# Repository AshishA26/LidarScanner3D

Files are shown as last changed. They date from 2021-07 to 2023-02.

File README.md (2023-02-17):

# LidarScanner3D

I designed and implemented a system from scratch which allows you to map a point cloud of your environment and nearby objects using LIDAR, Arduino, and Unreal Engine 4. 

I made the real time visualization tool using Unreal Engine and interfaced the LIDAR with an Arduino Mega using UART and I2C communication protocols.

In order for the Arduino to communicate with Unreal Engine 4, I used the "UE4Duino" plugin created by [RVillani](https://github.com/RVillani/UE4Duino).

Example scan of a sofa using a Lidar Lite-V3 (the white color in the middle is the location of the scanning system):
LiteV3LoadGif

Demonstration of the Lidar rotation with real-time mapping display:
ScanningGif

## Instructions to Run
- Hook everything up to the Arduino according to the [circuit  diagrams below](#circuit-diagrams)
- Upload the appropriate Arduino code, depending on which LIDAR you are using
- Run the `LidarScanner.exe` application, specify `Com Port`, `baud rate`, `scan type` and go from there

*Note: The `exe` is available in the releases of this repository.*

## Help/Tips
When trying to load a previously saved scan into Unreal Engine 4 project:
- Remember to rename the `.sav` file to `ScanDataSave.sav`
- The file goes in `.\LidarScanner3D\LidarScannerUE4\Saved\SaveGames`

When trying to load a previously saved scan into the compiled `LidarScanner.exe`:
- Go to `.\LidarScannerUE4Compiled\LidarScanner\Saved\SaveGames` and find `ScanDataSave.sav`
    - Note: This file has the point cloud data
- If wanted, copy or move it out into a different folder to keep for later and can rename it to something like `room.sav`
- To load back in, name the file as `ScanDataSave.sav` and move it to the `SaveGames` folder

## Mechanical Design 
Although I made the [first prototype out of wood](./Pics/LidarScannerPic5.jpg), the final design for the Lidar pan-and-tilt was hand built from Aluminum plates. It allows for easy portability, rotation, and great stability.

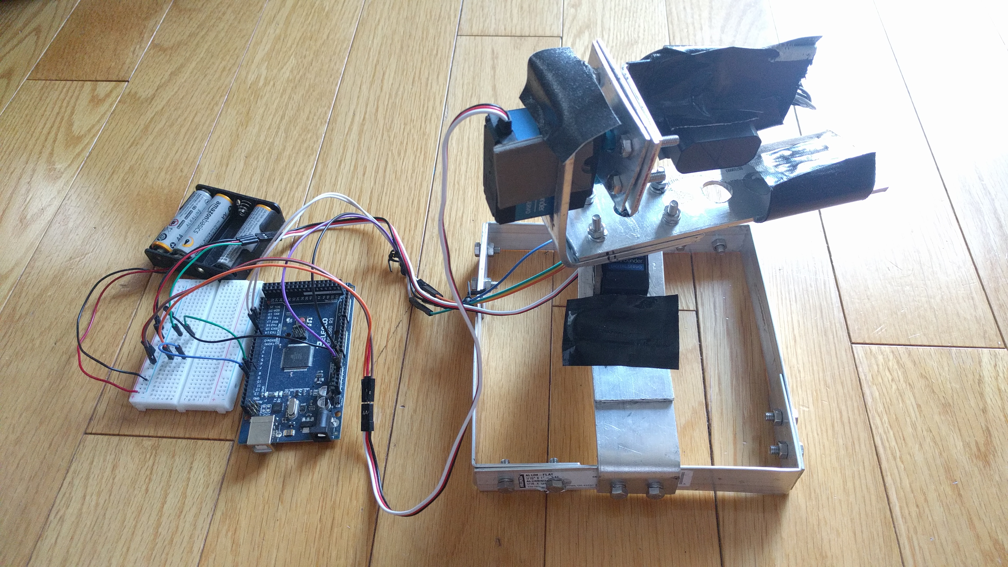
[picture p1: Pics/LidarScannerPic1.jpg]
LidarScannerPic1


There are 2 servos needed in order to achieve the scan. Servo 1 is placed right side up allowing the Lidar to rotate horizontally from side to side, and Servo 2 is placed sideways on Servo 1 allowing the Lidar to tilt vertically. To achieve a scan that fixes the tilt in the placement data, calculations have been done as shown [below](#point-calculations).

## Circuit Diagrams

I have interfaced the Lidar Lite V3 and TFMini Plus Lidar range finders with an Arduino Mega. I chose to do this using a perfboard for easy development and modularity. Some circuit schematics I made in Fritzing are shown below:

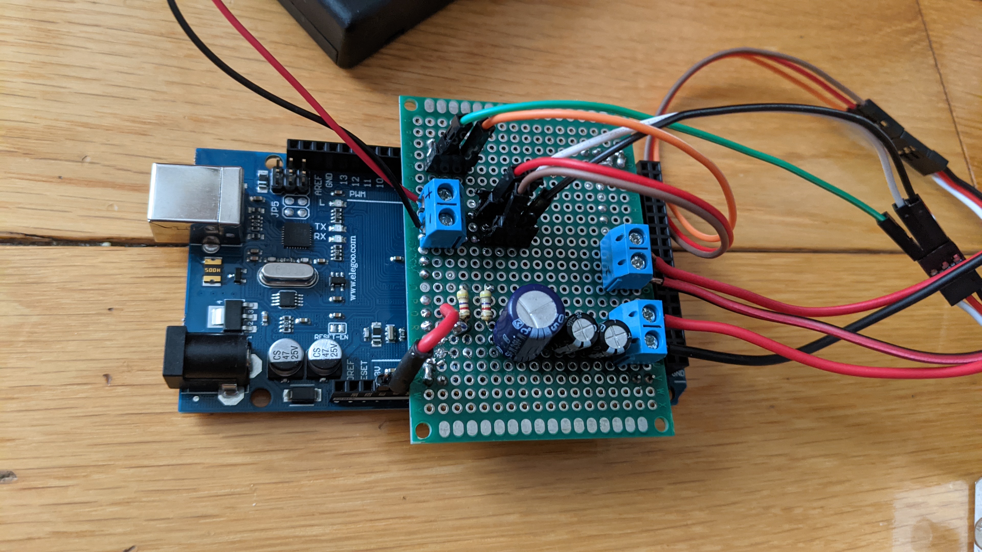
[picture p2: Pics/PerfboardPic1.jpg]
CircuitPicture


For Lidar Lite V3 using perfboard:
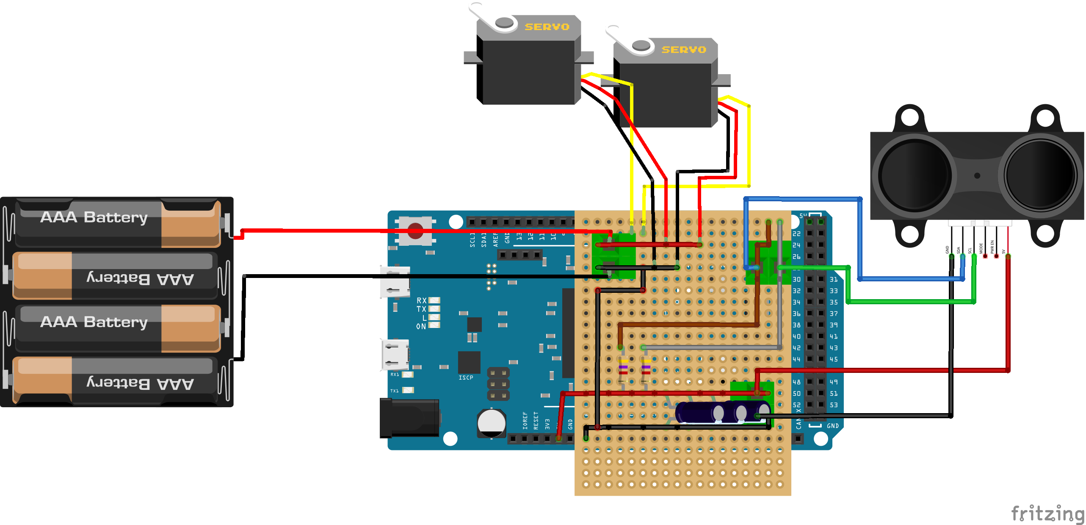
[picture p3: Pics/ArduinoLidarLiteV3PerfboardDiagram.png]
ArduinoLidarLiteV3PerfboardDiagram


For Lidar Lite V3 using breadboard:
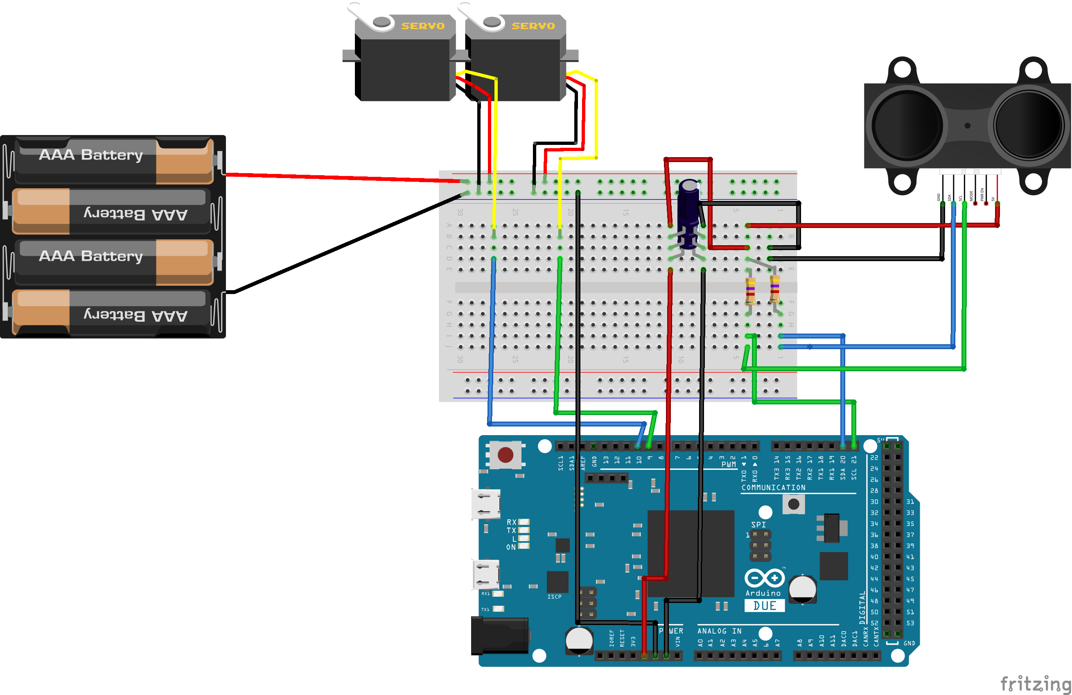
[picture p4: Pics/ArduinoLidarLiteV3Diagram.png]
ArduinoLidarLiteV3Diagram


For TFMini Plus:
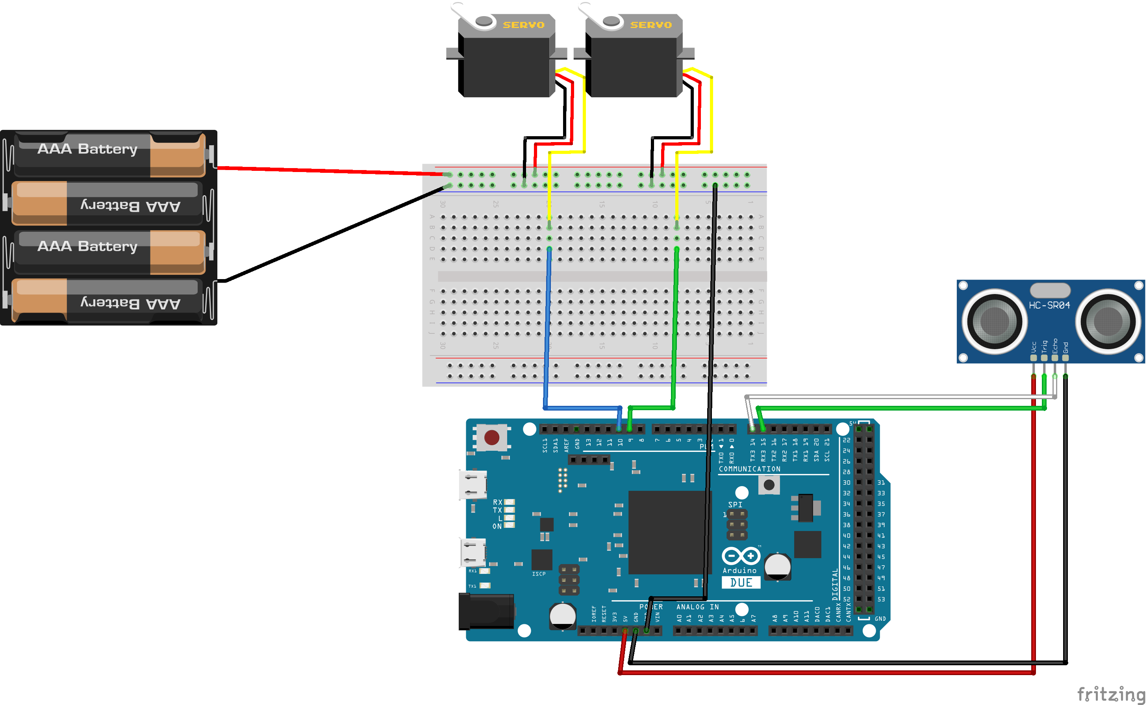
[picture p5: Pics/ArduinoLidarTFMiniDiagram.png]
ArduinoLidarTFMiniDiagram

 (Note: Replace the Sonar in the diagram with a TFMini Plus. The wiring from the TFMini Plus is based on the colors in the diagram).

For more pictures and diagrams, see the [Pics folder](https://github.com/AshishA26/LidarScanner3D/tree/main/Pics) of this repo.

## Point calculations
The LIDAR sensor measures a distance to the object, and the current orientation of this sensor is given by the servo positions. The angle calculations I did for finding the exact location of the point relative to the LIDAR in 3D Space using vector geometry are shown below:
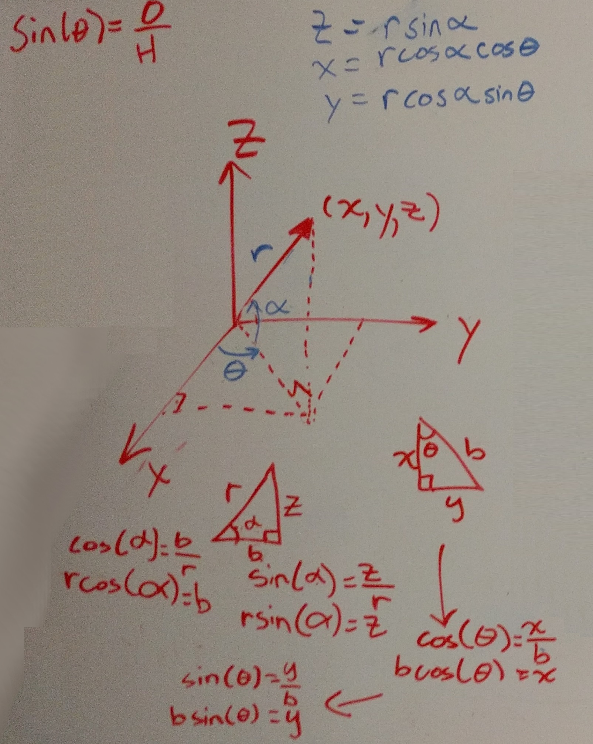
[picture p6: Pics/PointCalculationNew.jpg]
PointCalculation


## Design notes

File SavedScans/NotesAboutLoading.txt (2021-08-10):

When trying to load:
- Remember to rename the .sav file to ScanDataSave.sav
- It goes in \LidarScanner3D\LidarScannerUE4\Saved\SaveGames

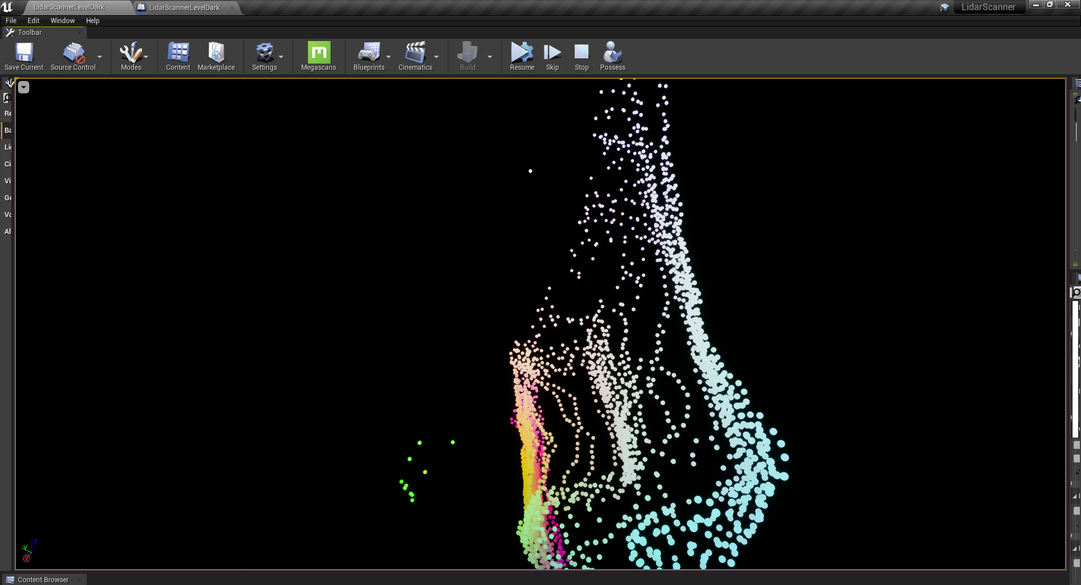
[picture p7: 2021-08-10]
Pics/Scans/sofa5b.png

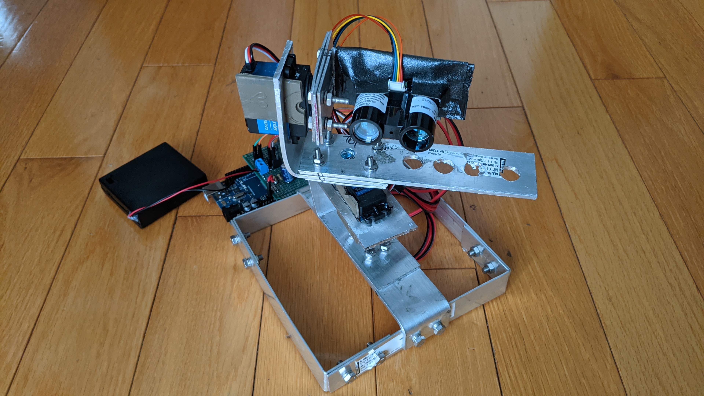
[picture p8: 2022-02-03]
Pics/LidarScannerPic2.jpg

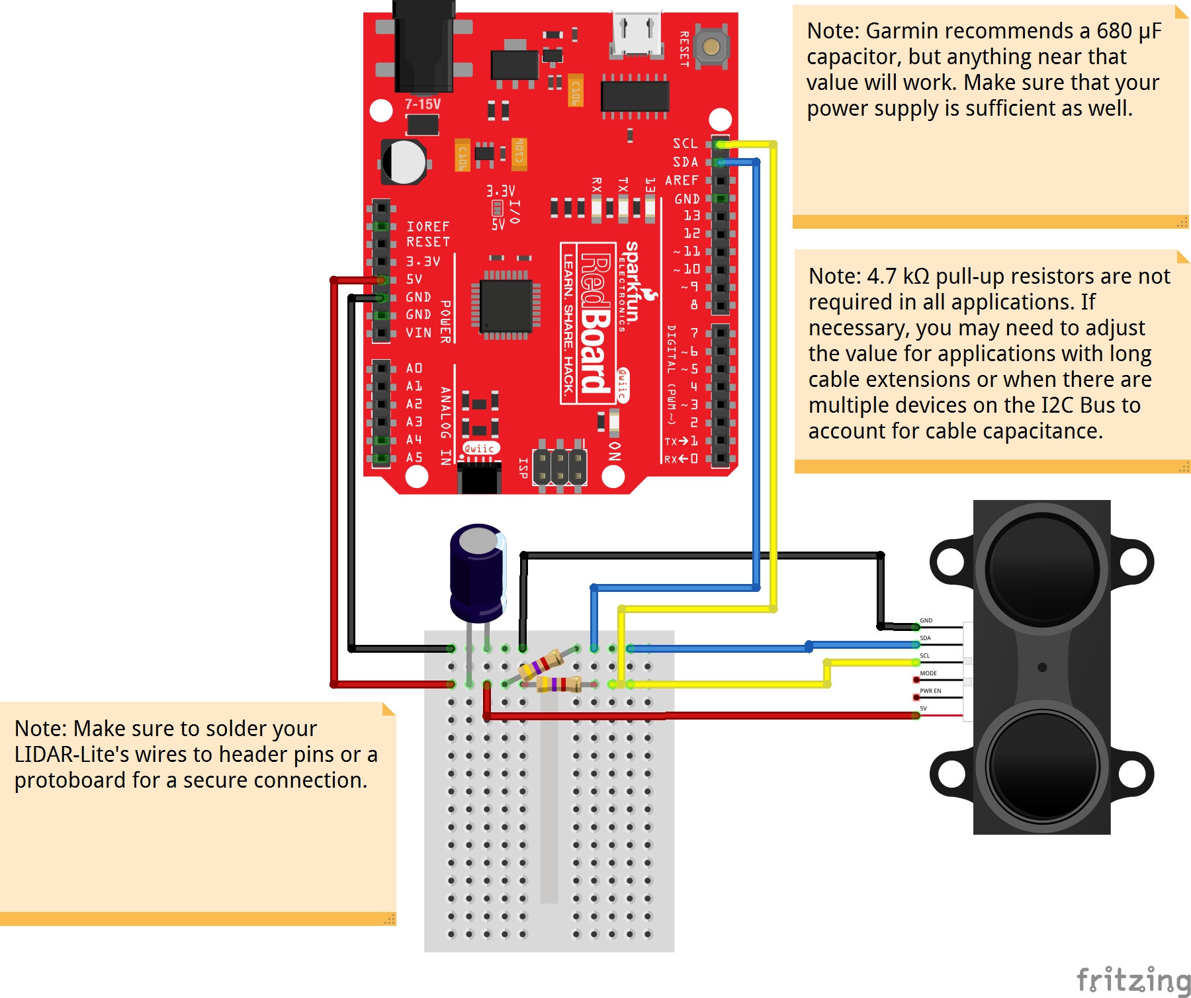
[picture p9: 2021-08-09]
Pics/SparkfunLidarV3Diagram.jpg

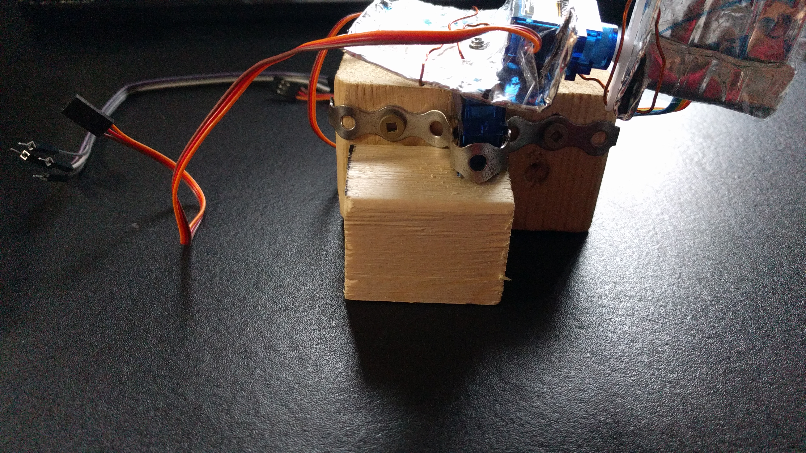
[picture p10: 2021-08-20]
Pics/LidarScannerPic3.jpg

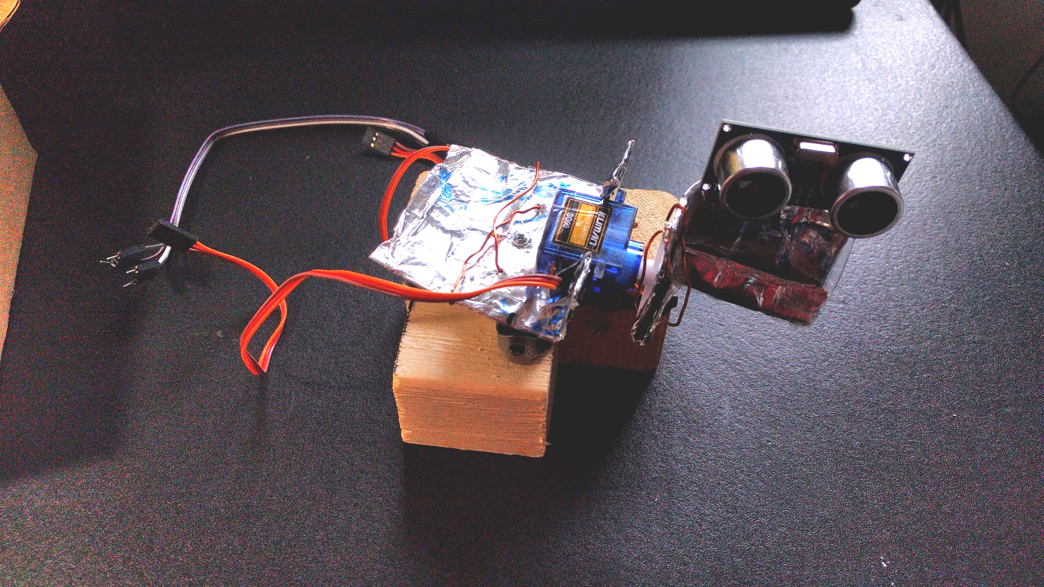
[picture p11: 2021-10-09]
Pics/LidarScannerPic5.jpg

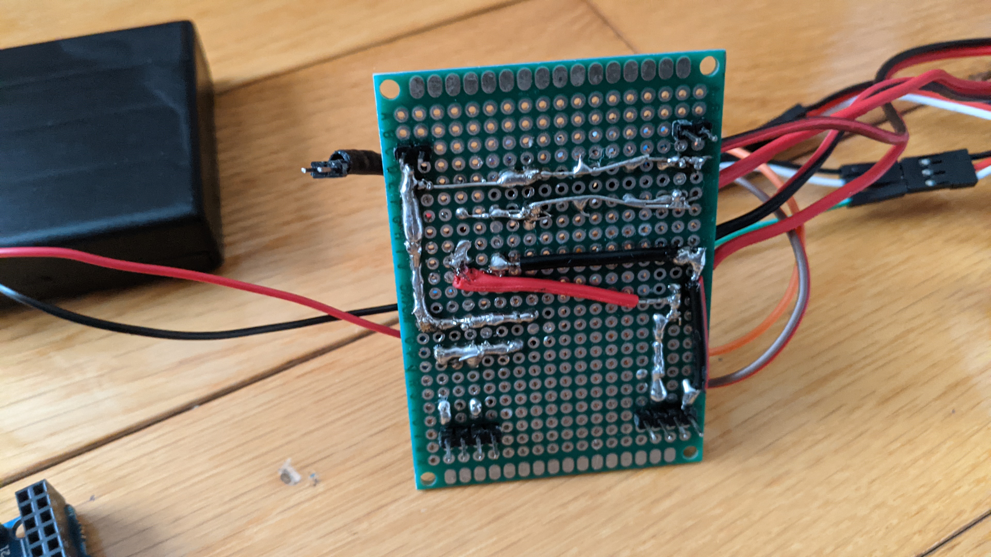
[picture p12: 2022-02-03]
Pics/PerfboardPic3.jpg

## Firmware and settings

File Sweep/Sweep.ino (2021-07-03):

///* Sweep
//  by BARRAGAN <http://barraganstudio.com>
//  This example code is in the public domain.
//
//  modified 8 Nov 2013
//  by Scott Fitzgerald
//  http://www.arduino.cc/en/Tutorial/Sweep
//*/
//
//#include <Servo.h>
//
//Servo myservo;  // create servo object to control a servo
//Servo myservo2;  // create servo object to control a servo
//// twelve servo objects can be created on most boards
//
//int pos = 0;    // variable to store the servo position
//
//void setup() {
//  myservo.attach(5);  // attaches the servo on pin 9 to the servo object
//    myservo2.attach(6);  // attaches the servo on pin 9 to the servo object
//}
//
//void loop() {
//  myservo.writeMicroseconds(500);              // tell servo to go to position in variable 'pos'
//  myservo2.writeMicroseconds(500); 
//  delay(2000);
//  myservo.writeMicroseconds(1500);              // tell servo to go to position in variable 'pos'
// myservo2.writeMicroseconds(1500); 
//  delay(2000);
//  myservo.writeMicroseconds(2500);              // tell servo to go to position in variable 'pos'
//  myservo2.writeMicroseconds(2500); 
//  delay(2000);
//}


//*************************************************3D RADAR CODE*************************************************//

// Include libraries:
#include <Servo.h>

Servo servo1;
Servo servo2;

// defines variables
int angle = 1000;
int verAngle = 2000;
long duration;
int distance;

void setup() {
  servo1.attach(5);
  servo2.attach(6);

  //Tell servo to go to this angle
  servo1.writeMicroseconds(angle);
  servo2.writeMicroseconds(verAngle);
  delay(1000);
}

void loop() {
  for (angle = 1000; angle <= 2000; angle += 5)
  {
    servo1.writeMicroseconds(angle);
    delay(10);
  }
  MoveUp();
  for (angle = 2000; angle >= 1000; angle -= 5)
  {
    servo1.writeMicroseconds(angle);
    delay(10);
  }
  MoveUp();
}
//Move vertical servo up by one degree
void MoveUp() {
  verAngle = verAngle - 5;
  servo2.writeMicroseconds(verAngle);
  delay(10);
}

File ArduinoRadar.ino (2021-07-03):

//*************************************************3D RADAR CODE*************************************************//

// Include libraries:
#include <Servo.h>
#include<SoftwareSerial.h>
//Create serial object;
SoftwareSerial mySerial(10, 9); //Set Transmit and Recieve pins, pin 2 is RX, pin 3 is TX
// Create a new servo object:
Servo servo1;
Servo servo2;


// Define the servo pin:
//int servo1Pin = 9;
//int servo2Pin = 10; THESE WERE SOMEHOW CAUSING THE PROBLEM OF THE 2 BIG SERVOS NOT TO WORK, ONLY ONE OF THEM HAD WORKED

int dist;
int strength;
int check;
int uart[9];
int i;
const int HEADER = 0x59;

// defines variables
int angle = 500;
int verAngle = 2000;
long duration;
int distance;
int pointArray[3];
int mapAngle;
int mapVerAngle;
int mapStartVerAngle;

void setup() {
  Serial.begin(115200); // Starts the serial communication
  mySerial.begin(115200);
  Serial.print("start");

  // Attach the Servo variable to a pin:
  servo1.attach(5);
  servo2.attach(6);

  //Tell servo to go to this angle
  servo1.writeMicroseconds(angle);
  servo2.writeMicroseconds(verAngle);
  pointArray[0] = 0;

  mapStartVerAngle = verAngle;
  mapStartVerAngle = map(mapStartVerAngle, 500, 2500, 0, 180);

  pointArray[1] = mapStartVerAngle;
  delay(1000);
}

void loop() {
  // Sweep from 0 to 2500 degrees:
  for (angle = 500; angle <= 2500; angle += 5)
  {
    Sonar();
    mapAngle = angle;
    mapAngle = map(mapAngle, 500, 2500, 0, 180);
    printArray();
    pointArray[0] = mapAngle;
    servo1.writeMicroseconds(angle);
    delay(10);
  }
  MoveUp();
  // And back from 2500 to 0 degrees:
  for (angle = 2500; angle >= 500; angle -= 5)
  {
    Sonar();
    mapAngle = angle;
    mapAngle = map(mapAngle, 500, 2500, 0, 180);
    printArray();
    pointArray[0] = mapAngle;
    servo1.writeMicroseconds(angle);
    delay(10);
  }
  MoveUp();
}
//Move vertical servo up by one degree
void MoveUp() {
  verAngle = verAngle - 5;
  servo2.writeMicroseconds(verAngle);
  mapVerAngle = verAngle;
  mapVerAngle = map(mapVerAngle, 500, 2500, 0, 180);
  pointArray[1] = mapVerAngle;
  delay(10);
}

void Sonar() {
  if (mySerial.available()) {
    if (mySerial.read() == HEADER) {
      uart[0] = HEADER;
      if (mySerial.read() == HEADER) {
        uart[1] = HEADER;
        for (i = 2; i < 9; i++) {
          uart[i] = mySerial.read();
        }
        check = uart[0] + uart[1] + uart[2] + uart[3] + uart[4] + uart[5] + uart[6] + uart[7];
        if (uart[8] == (check & 0xff)) {
          dist = uart[2] + uart[3] * 256;
          strength = uart[4] + uart[5] * 256;
          Serial.print(dist);
          Serial.print('\n');
          delay(0);
          pointArray[2] = dist;
        }
      }
    }
  }
}

void printArray() {
  for (int i = 0; i < 3; i++) {
    Serial.print(pointArray[i]);
    if (i != 2) {
      Serial.print(" ");
    }
  }
  Serial.println();
}

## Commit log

2021-06-14 Setup python and arduino communcations
2021-06-22 working on stronger servos
2021-06-24 fixed data to graph problem
    [ArduinoRadar.ino]
2021-06-25 Did sonar angle math
2021-07-03 Changed servo PWM delay to 10 ms
    0 ms was causing the servo to glitch and it was going 360 degree
    rotation - too fast for the servo to handle
    [ArduinoRadar.ino, LIDARtest.ino, Sweep.ino]
2021-07-11 Fixing math for 3d mapping
    [LidarScanner3D.pde, LidarScanner3D.py]
2021-07-11 Fixed 3d point math
    [LidarScanner3D.pde]
2021-07-15 Calibrating servos
2021-07-18 Fixed spikes and smoothed Lidar data
2021-08-08 added schematic diagram
    [ArduinoLidarTFMiniDiagram.fzz]
2021-08-08 adding functionality for lidar lite v3
2021-08-09 Added code for garmin lidar lite v3
    [ArduinoLidarLiteV3Diagram.fzz]
2021-08-09 added lidar lite v3 circuit diagram
    [ArduinoLidarLiteV3Diagram.fzz]
2021-08-13 added gui and fixed many bugs
    [LidarScannerLiteV3.ino]
2021-08-13 added fixes to TFMini code
    [LidarScannerLiteV3.ino, LidarScannerTFMini.ino]
2021-08-13 Fixed button
2021-08-20 added perfboard diagram
    [ArduinoLidarLiteV3Diagram.fzz, ArduinoLidarLiteV3PerfboardDiagram.fzz]
2021-08-20 Added perfboard diagram and old frame pics
